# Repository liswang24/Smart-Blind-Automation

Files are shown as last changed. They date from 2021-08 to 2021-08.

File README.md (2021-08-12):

# Smart Blind Attachment Controlled via Google Assistant

## About

This project allows for the control of a roller blind with a ball chain lift cord through the Google Assistant. The blind attachment device simply attaches to the base of the blind's lift cord to move the blinds without altering the blinds themselves - making it versatile to a wide range of blinds and renter friendly.

The project utilizes the [SinricPro Library](https://github.com/sinricpro/esp8266-esp32-sdk) to connect the device to the Google Home. SinricPro allows for the blinds to be set to any percentage position relative to the fully open position through the Google Assistant.

The device is controlled using an ESP32 Development Board. A rotary encoder is used to measure the position of the blinds and a 12V motor and motor driver is used to move the blinds up and down. A 12V AC/DC wall plug power supply powers the device. A 3D printed gear turns the lift cord and the 3D printed housing secures the components and allows for attachment to a peripheral wall.

Video demonstrating the device in action:

Video link demonstrating device (https://www.youtube.com/watch?v=RJqdqQGxrRk)

## Installation and Setup

### Materials

 Hardware | Software | Other
----------|----------|---------
 [ESP32 Development Board](https://www.amazon.ca/gp/product/B08HJYT6YV/ref=ppx_yo_dt_b_asin_title_o04_s00?ie=UTF8&psc=1) + Micro USB Cord | Arduino IDE | 2.4G Wifi Connection
 [Rotary Encoder](https://www.amazon.ca/gp/product/B07T3672VK/ref=ppx_yo_dt_b_asin_title_o01_s00?ie=UTF8&psc=1) | SinricPro Account | 3D Printer + Materials
 [12V Motor](https://www.amazon.ca/gp/product/B07MW5NH3P/ref=ppx_yo_dt_b_asin_title_o07_s00?ie=UTF8&psc=1) | Google Account |
 [12V AC/DC Power Supply](https://leeselectronic.com/en/product/14361-14361POWERSUPPLYACDCSWITCHING12V.html) |  |
 [LM2596 Buck Converter](https://www.amazon.ca/gp/product/B08Q2YKJ6Q/ref=ppx_yo_dt_b_asin_title_o04_s00?ie=UTF8&psc=1)|  |
 [L293D H-Bridge](https://leeselectronic.com/en/product/71198-h-bridge-l293d-quadruple-half-h-driver-w-diode.html)|  |
 Breadboard and/or Prototype Board|  |
 DC Barrel Power Jack/Connector |  |
 2 x 10Ω Resistors |  |
 Header Pins|  |
 Wires|  |
 Solder & Soldering Iron |  |
 8 x M2.6 x 12 Screws |  |
 8 x M2.6 Nuts |  |
 4 x #4 3/8 Screws |  |
 2 x #8 Drywall Screws (optional for mounting) |  |

### Creating a SinricPro Device and Adding it to the Google Home

Login or create a [SinricPro](https://sinric.pro) account. Once logged in, select 'Devices' from the menu on the left. Click the '+ Add Device' button at the top to create a new device. Fill out the necessary fields in the form. Select the device type to be 'Blinds'. After this you should see a Blinds Device under your devices. It will have a device ID associated with it, we will need this later.

SinricPro Device ID

You will also need an APP KEY and APP SECRET, these can be found under 'Credentials' in the menu.

Now we need to add this new device to the Google Home. Open up the Google Home app and login or create an account. To add a new device, click the '+' in the upper left corner and select 'Set up device', search for SinricPro and log in with your account created previously. Now the blinds device should show up in your Google Home.
| | | | |
|---|---|---|---|
| Add Device | Setup Device | SinricPro Device | Blinds Device |

[Add]:https://user-images.githubusercontent.com/43894278/129123121-1c7fbf13-0b3f-4c2b-bfda-c5d1e9050c8d.jpeg
[Setup]:https://user-images.githubusercontent.com/43894278/129123118-c7fe638c-03c7-4255-ad61-9228a8d68329.jpeg
[SinricPro]:https://user-images.githubusercontent.com/43894278/129123114-1d81cac8-5e72-4d91-b5ae-dbc3ea34b52b.jpeg
[Blinds Device]:https://user-images.githubusercontent.com/43894278/129123108-21d57ef4-c113-431b-aa01-f2a6fb04d991.jpeg

### Assembling the Circuit Board

For development I used a breadboard to ensure each component was working correctly both individually and when connected to the system. After ensuring everything worked, I proceeded to solder everything down to a prototyping board for more secure connections and to be more compact. I attached components from both sides of the prototyping board and lifted up the ESP32 board using header pins so that the space below the board could be utilized (I slipped the h-bridge into the space below). The pinouts specifications I used can be found in pinout.h and coupled with the breadboard image attached below, these pinouts can be modified but please refer to the ESP32 datasheet to see which pins are available to be used.
| | |
|---|---|
| Breadboard | Components w/o casing |

[Breadboard]:https://user-images.githubusercontent.com/43894278/129124386-88116fc0-2475-4e6f-8962-7667ef1d4fc5.jpg
[Components]:https://user-images.githubusercontent.com/43894278/129124280-c7530961-9761-438b-a6c2-8497b6fc0ed1.JPG

#### Modifying the Code

##### credentials.h

credentials.h will need to be updated with the information pertaining to your specific device and wifi connection. The SinricPro credentials from setting up the device on the SinricPro site are to be used here.

    // Wifi Network Credentials
    #define WIFI_SSID "YOUR-WIFI-NAME"
    #define WIFI_PASSWORD "YOUR-WIFI-PASSWORD"

    // Sinric Pro Credentials
    #define APP_KEY    "YOUR-SINRICPRO-APP-KEY"
    #define APP_SECRET "YOUR-SINRICPRO-APP-SECRET"
    #define BLINDS_ID  "YOUR-DEVICE-ID"

##### pinout.h

If you have chosen to use different pinouts on the ESP32 board, those will need to be updated in pinout.h. Here you can also modify the baud rate and speed of the motors.

The FULLY_OPEN parameter will need to be modified to cater to your specific blinds. I recommend initially setting it a low value (i.e. 50), testing how far it lifts and adjust accordingly.

You may also need to swap the MOTOR_IN_1/MOTOR_IN_2 and OUTPUT_A/OUTPUT_B pins based on how the motor and encoder is wired up.

#### Uploading the Code to the ESP32 Board

[Install Arduino ESP32 support](https://docs.espressif.com/projects/arduino-esp32/en/latest/installing.html#installing-using-boards-manager) using the Boards Manager in the [Arduino IDE](https://www.arduino.cc/en/software).

Connect the ESP32 board via the micro USB to your computer, select the correct 'Port' for your board and select the 'Board'.
Arduino IDE Settings

Open the Smart_Blinds_Automation folder in your Arduino IDE and upload to the ESP32 board.

### Printing the Parts

The 3 parts which need to be printed can be found in the "3D Print Parts" folder in the repository. You can print these STL parts however you wish.

| Ball Chain Gear | Right Half of Housing | Left Half of Housing |
|---|---|---|
| Ball Chain Gear Print | Housing Right Side Print | Housing Left Side Print |

[Ball Chain Gear]:https://user-images.githubusercontent.com/43894278/129276851-ae819818-c09c-4f16-91a0-c309d7a51a9e.png
[Housing Right Side]:https://user-images.githubusercontent.com/43894278/129276882-c094b97b-f291-41ab-890c-8283fea8f1e8.png
[Housing Left Side]:https://user-images.githubusercontent.com/43894278/129276932-3de41852-87c2-476e-9ebe-7712eba964d2.png

I designed these parts using [OnShape](https://www.onshape.com/en/). The Ball_Chain_Gear part is based from the [Bead Chain Gear](https://www.thingiverse.com/thing:38006) by [adgaudio](https://www.thingiverse.com/adgaudio/designs) and modified to attach onto the encoder and motor.

#### Resin Printing

I resin printed these parts using the [VOXELAB Polaris 3D Printer](https://www.amazon.ca/gp/product/B08FFZG73H/ref=ppx_yo_dt_b_search_asin_title?ie=UTF8&psc=1) This is a lower cost resin printer and pretty beginner friendly. (Here is a [helpful video](https://www.youtube.com/watch?app=desktop&v=XSlofiAx4c0) by 'A Review From The Top' on YouTube to get started with this printer)

For these prints I used the [ANYCUBIC Clear Resin](https://www.amazon.ca/gp/product/B08NG67MMB/ref=ppx_yo_dt_b_asin_title_o00_s00?ie=UTF8&th=1) since it was what I had on hand. You may want to use a solid coloured resin to match ur wall or blinds colour to minimize the look of the housing.

To slice my prints I used [VoxelPrint](https://www.voxelab3dp.com/download). I lifted my print off of the print bed ~8mm to allow for easier removal from the build plate when printing. Since the printer I have is rather small, I opted to slice each of my housing parts in half and print them separately. This allowed to save some wasted material on supports as well. I used VoxelPrint to auto-generate my supports (If your supports are printing but not the part itself, thicken the width of the support a bit). It took ~8 hrs to print each of the parts and I secured the two halves together by painting some resin on the connection points and quickly curing it with a UV LED nail lamp I had. Print Supports

### Assembly and Installation

| | | |
|---|---|---|
| Component Mounting | Component Mounting Beneath | Fully Assembled Device |

[Component Mounting]:https://user-images.githubusercontent.com/43894278/129278276-876c11e0-9c07-4530-933e-0890ee077a50.JPG
[Component Mounting Beneath]:https://user-images.githubusercontent.com/43894278/129278286-e5b35b19-2e36-4f46-9218-ef14dd44472c.JPG
[Fully Assembled Device]:https://user-images.githubusercontent.com/43894278/129279991-e84d9d57-5636-4897-bd64-bbba73b362a9.jpeg

To assemble the device together, first secure the encoder and ESP32 board to the posts on left side of the housing using the M2.6 screws and nuts. Then press the header pins on the circuit board onto the ESP32 to secure the board. Feed the 12V power cable through the opening on the bottom. The ball chain gear can now be slid onto the encoder with the flat side facing in toward the encoder. The blind cord is then to be slid into the teeth of the gear and pass through the two holes located on the top of the part.

The motor is to be tucked beneath the arms on the right half of the housing and secured to the four holes using the #4 screws. Finally, place two of the nuts into the hexagonal spots left on the left side of the housing and now close the right half of the housing left half with the motor shaft inside the ball chain gear part. Align the screws in the center and secure it with two M2.6 screws. Additionally, two holes on the top and bottoms of the housing can be used to mount the device to the wall.

## Future Improvements

* Replace motor for a motor with more torque to be used on larger/heavier blinds.
* Replace motor with "embedded/attached" encoder to minimize space/decrease bulk of housing (sleeker look).
* Create and manufacture PCB board to further minimize size.
* Implement a way to setup 'FULLY_OPEN' position via hardware (button upon boot etc.)

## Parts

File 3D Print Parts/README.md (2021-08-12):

Housing_encoder+ESP32.stl & Housing_motor.stl connect together to fully house circuity and components and mounts to wall.
Ball_chain_gear.stl modified from Bead Chain Gear created by adgaudio (https://www.thingiverse.com/thing:38006) to attach to encoder and motor.

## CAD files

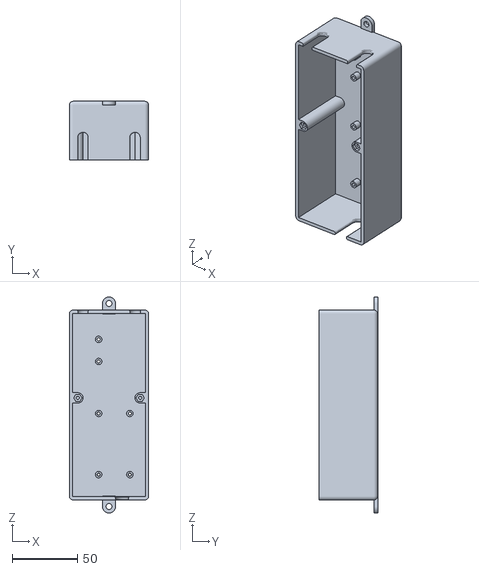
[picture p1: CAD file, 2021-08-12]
3D Print Parts/Housing_encoder+ESP32.stl
61.0 x 45.0 x 166.0

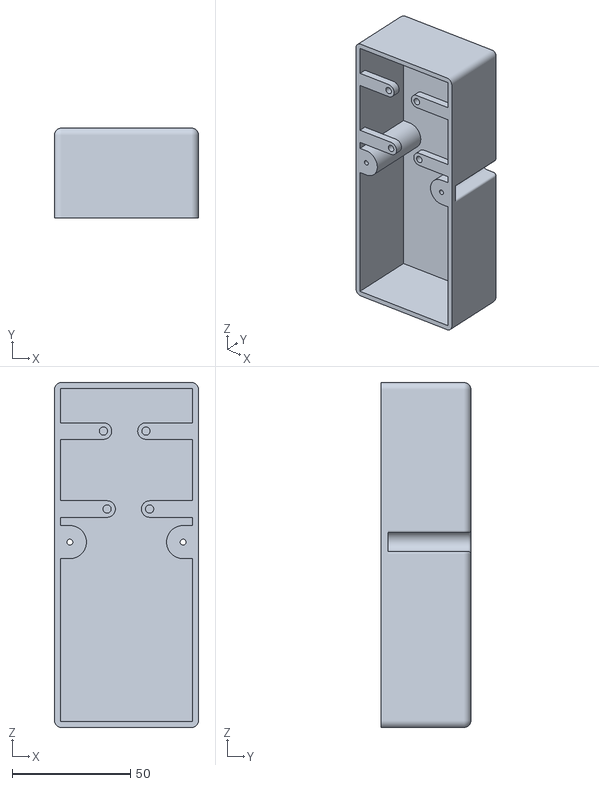
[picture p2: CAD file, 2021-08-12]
3D Print Parts/Housing _motor.stl
61.0 x 38.0 x 146.0

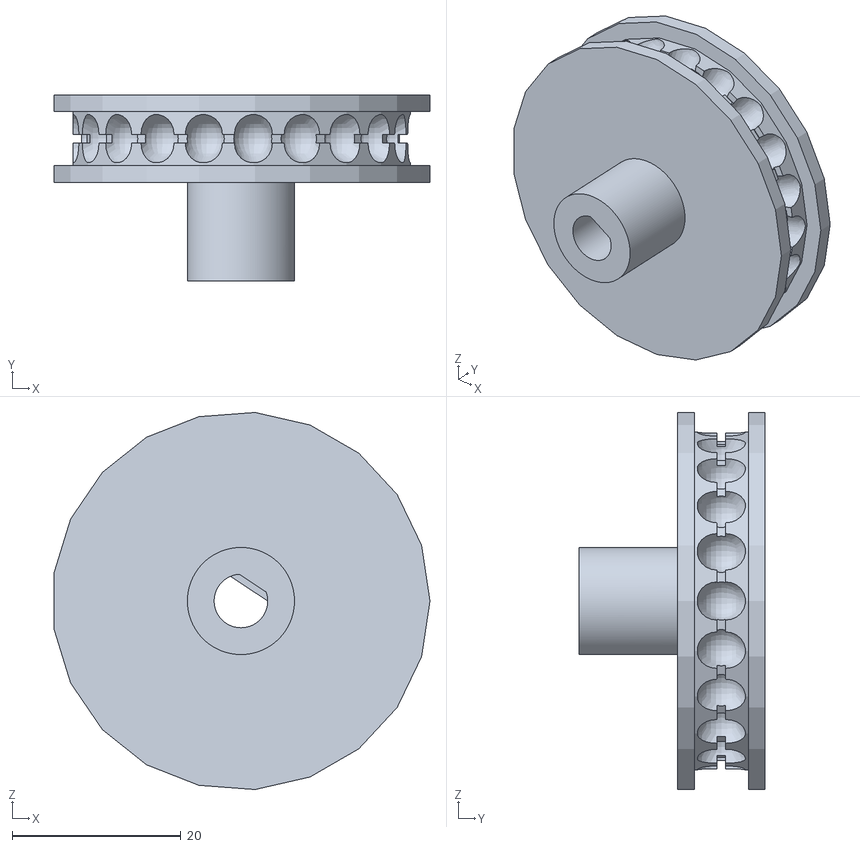
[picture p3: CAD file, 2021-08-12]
3D Print Parts/Ball_chain_gear.stl
44.6 x 22.1 x 44.7

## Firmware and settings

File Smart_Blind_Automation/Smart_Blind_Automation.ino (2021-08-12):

#include <WiFi.h>
#include <SinricPro.h>
#include "SinricProBlinds.h"
#include "credentials.h"
#include "pinout.h"

double blindsPosition        = 0;
double desiredBlindsPosition = 0;

// Encoder
double currStateA;
double prevStateA;
double currStateB;

void setup()
{
  // Set Pin Modes
  pinMode(MOTOR_SPEED, OUTPUT);   // Motor
  pinMode(MOTOR_IN1, OUTPUT);     // .
  pinMode(MOTOR_IN2, OUTPUT);     // .
  pinMode (OUTPUT_A,INPUT);       // Encoder
  pinMode (OUTPUT_B,INPUT);       // .

  // ISR Encoder
  prevStateA = digitalRead(OUTPUT_A);  //read initial state of OUTPUT_A
  attachInterrupt(digitalPinToInterrupt(OUTPUT_B), updatePosition, CHANGE);

  Serial.begin(BAUD_RATE);

  setupWifi();
  setupSinricPro();
}

void loop () {
  // Handle connection between SinricPro server and device
  SinricPro.handle();
}

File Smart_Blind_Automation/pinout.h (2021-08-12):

// Motor Pins
#define MOTOR_SPEED     27
#define MOTOR_IN1       26
#define MOTOR_IN2       25

// Encoder Pins
#define OUTPUT_A         33
#define OUTPUT_B         32

// Serial Monitor
#define BAUD_RATE      9600

// Motor Speed
#define SPEED           128     // Slow = 64, Normal = 128, Fast = 255

// Postions
#define FULLY_OPEN      250     // Modify based on desired blind length

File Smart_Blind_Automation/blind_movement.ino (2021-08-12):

void moveBlindsUp(void){
  digitalWrite(MOTOR_SPEED, SPEED);
  digitalWrite(MOTOR_IN1, LOW);
  digitalWrite(MOTOR_IN2, HIGH);
}
 
void moveBlindsDown(void){
  digitalWrite(MOTOR_SPEED, SPEED);
  digitalWrite(MOTOR_IN1, HIGH);
  digitalWrite(MOTOR_IN2, LOW);
}

void stopBlinds(void){
  digitalWrite(MOTOR_IN1, LOW);
  digitalWrite(MOTOR_IN2, LOW);
}

void moveBlindsToDesiredPosition(int desiredPosition) {
  Serial.print("Moving blinds to: ");
  Serial.println(desiredPosition);

  while (blindsPosition < desiredPosition) {
    Serial.println("Moving blinds up!");
    Serial.print("Current Position: ");
    Serial.println(blindsPosition);

    moveBlindsUp();
  }
  
  while (blindsPosition > desiredPosition) {
    Serial.println("Moving blinds down!");
    Serial.print("Current Position: ");
    Serial.println(blindsPosition);

    moveBlindsDown();
  }
}

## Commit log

2021-07-23 Added implementation for encoder position reading and motor control
2021-08-10 Change direction of motors after mounting and adjust position
2021-08-11 Create new folder for 3D printed parts
2021-08-11 Add files for housing and encoder parts
    [Ball_chain_gear.stl, Housing _motor.stl, Housing_encoder+ESP32.stl]
2021-08-11 Delete Ball_chain_gear.stl
    incorrect file uploaded
    [Ball_chain_gear.stl]
2021-08-11 Add ball chain gear print
    [Ball_chain_gear.stl]
2021-08-12 small fix for variable naming
    [Smart_Blind_Automation.ino, pinout.h]
